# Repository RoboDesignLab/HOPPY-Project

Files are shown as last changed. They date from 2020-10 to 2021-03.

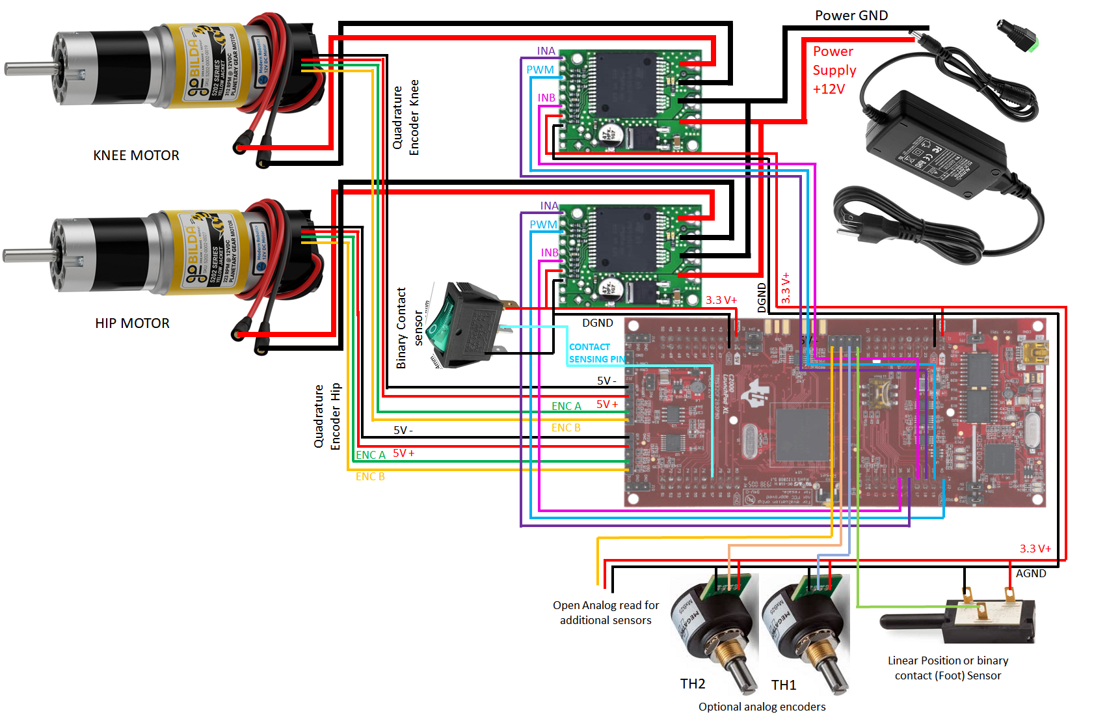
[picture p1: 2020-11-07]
wiring_diagram_HOPPY.png

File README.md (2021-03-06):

# ------------------------HOPPY-Project------------------------
## HOPPY: An Open-source Kit for Education with Dynamic Legged Robots
HOPPY 2
----------------------------------------------------------------------------------------------------------------------------
## CONTENTS OF THIS FILE
---------------------
* Introduction
* General Notes
* Setting up CCS 
* CAD 
* Simulator

## Introduction
------------
The project is an open-source, low-cost, robust, and modular kit for robotics education. The robot, HOPPY, dynamically hops around a fixed gantry. The kit targets lowering the barrier for studying dynamic robots and legged locomotion in real systems. Controlling dynamic motions in real robots present unique challenges to the software and hardware which are often overlooked in conventional robotics courses. This project describes the topics which can be studied using the kit, lists its components, discusses best practices for implementation, presents results from experiments with the simulator and the real system, and suggests further improvements. HOPPY was utilized as the topic of a semester-long project for the Robot Dynamics and Control course at the University of Illinois at Urbana-Champaign. Students provided a positive feedback from the hands-on activities during the course and the instructors will continue to develop and improve the kit for upcoming semesters.

Find out more in our overview paper: https://arxiv.org/pdf/2010.14580.pdf

Assembly instructions can be found here: https://youtu.be/CDxhdjob2C8

See the robot in action here:
https://youtu.be/_lbKIpiRWKI
https://www.youtube.com/watch?v=AvJIx4CQarM

-----------------------------------------------------------------------------------------------------------------------------
## General Notes
-------------
DO NOT run the given code to the motors while they are attached to the leg. This code is meant to show a given code flow and test the motors, board, and program setup. Clamp the motors down and run the code on them externally. 

Depending on how the leg is assembled, you may need to adjust the lengths used in the code. More instructions re inside the general definitions section of the program.

----------------------------------------------------------------------------------------------------------------------------
## Setting up Code Composer Studio (CCS) and the programming enviroment
--------------------------------------------------------------------
CCS is the IDE for TI products and is an easy to sude system. A introduction to CCS can be found at the following link: https://www.youtube.com/watch?v=11lsNYW7zkw&ab_channel=CodeComposer

Hoppy was implemented using version 8 of CCS which can be downloaded at the following link: http://software-dl.ti.com/ccs/esd/documents/ccs_downloads.html. The instructions for installing the software can be found at the second link. 

Once CCS in installed, unzip the Blinky_rtos_FLASHCCS8.zip folder and open the project in CCS. This project should blink an LED on the board after it is flashed onto the board. cpu01_main.c is the main file that you will be working in; this is also the file that you should be in when you build and debug the program.

Once the programming enviroment is working, the file cpu01_main_EXAMPLE.c can be coppied into cpu01_main.c. This program is a starting point for the user to program. It includes an intuitive code structure, working PD control on the hip and knee motors, and contact sensing (analog and binary). The instructions to use the code setup and the different sensing options is in the file with line numbers for each part in the code. 

The wiring diagram that shows how hook up the system is also included in the folder.

----------------------------------------------------------------------------------------------------------------------------
## CAD
---

The CAD models of the entire setup are inlcuded in SolidWorks and .STEP formats. Video  instructions for mechanical assembly can found at the following link: https://youtu.be/CDxhdjob2C8

The Bill of Materials (BOM), a complete list of components and quantities, is also listed in the folder. 

-----------------------------------------------------------------------------------------------------------------------------
## Simulator
---------

### Requirement
MATLAB and MATLAB optimization toolbox

### Installation
There is no need to install external packages.

### Usage
Navigate to the folder "Simulator_MATLAB" and set the working directory of MATLAB to be this directory. To start the simulation, run the file
```
...\Simulator_MATLAB\MAIN.m
```
If the code works properly, the following GUI will show up and a video file will be generated.



Please refer to the Code_Instruction.pdf file to navigate through each component of this simulator

If you encounter any problems regarding the simulator, please raise an issue under this repo.

Enjoy!
-----------------------------------------------------------------------------------------------------------------------------

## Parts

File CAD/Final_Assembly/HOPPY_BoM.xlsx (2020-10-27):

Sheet: Base
Index | Part Number | Quantity | Price per unit (USD) | Link
0.1 | 1140-0006-0144 | 1 | 12.99 | https://www.gobilda.com/1140-series-aluminum-baseplate-6mm-thickness-144mm-diameter/
0.2 | 4103-0032-0144 | 1 | 3.89 | https://www.gobilda.com/4103-series-gotube-144mm-length/
0.3 | 1604-0043-0032 | 2 | 12.99 | https://www.gobilda.com/1604-series-2-side-2-post-pillow-block-32mm-bore/
0.4 | 1500-0010-0032 | 1 | 0.1658333333 | https://www.gobilda.com/1500-series-plastic-spacer-32mm-id-x-34mm-od-1mm-thickness-12-pack/
0.5 | 1506-0032-0004 | 1 | 1.495 | https://www.gobilda.com/1506-series-32mm-id-spacer-36mm-od-4mm-length-2-pack/
0.6 | 1506-0032-0006 | 2 | 1.645 | https://www.gobilda.com/1506-series-32mm-id-spacer-36mm-od-6mm-length-2-pack/
0.7 | 2800-0004-0010 | 4 | 0.1356 | https://www.gobilda.com/2800-series-zinc-plated-steel-socket-head-screw-m4-x-0-7mm-10mm-length-25-pack/
0.8 | 98035A102 | 4 | 0.472 | https://www.mcmaster.com/98035A102/
0.9 | 2802-0004-0008 | 4 | 0.1276 | https://www.gobilda.com/2802-series-zinc-plated-steel-button-head-screw-m4-x-0-7mm-8mm-length-25-pack/

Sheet: Link 1
Index | Part Number | Quantity | Price per unit (USD) | Link | Notes
1.1 | 1123-0048-0144 | 2 | 4.29 | https://www.gobilda.com/1123-series-pattern-plate-1-x-5-hole-48-x-144mm/
1.2 | 1121-0003-0096 | 1 | 2.89 | https://www.gobilda.com/1121-series-low-side-u-channel-3-hole-96mm-length/
1.3 | 2803-0039-0007 | 2 | 1.995 | https://www.gobilda.com/2803-series-stainless-steel-threaded-plate-39-7-2-pack/
1.4 | 1502-0006-0020 | 4 | 0.2975 | https://www.gobilda.com/1502-series-4mm-id-spacer-6mm-od-2mm-length-4-pack/
1.5 | 1502-0006-0030 | 4 | 0.3225 | https://www.gobilda.com/1502-series-4mm-id-spacer-6mm-od-3mm-length-4-pack/
1.6 | 2800-0004-0010 | 20 | 0.1356 | https://www.gobilda.com/2800-series-zinc-plated-steel-socket-head-screw-m4-x-0-7mm-10mm-length-25-pack/
1.7 | 1401-0043-0032 | 2 | 5.99 | https://www.gobilda.com/1401-series-2-side-2-post-clamping-mount-43mm-width-32mm-bore/
1.8 | 1506-0032-0004 | 4 | 1.495 | https://www.gobilda.com/1506-series-32mm-id-spacer-36mm-od-4mm-length-2-pack/
1.9* | 1400-0032-0032 | 2 | 5.99 | https://www.gobilda.com/1400-series-1-side-2-post-clamping-mount-32mm-bore/ | *Only required if utilizing encoder on jount 2.
1. 10 | 4103-0032-0043 | 2 | 2.99 | https://www.gobilda.com/4103-series-gotube-43mm-length/
1.11 | 1603-0032-0032 | 2 | 12.99 | https://www.gobilda.com/1603-series-face-thru-hole-pillow-block-32mm-bore/
1.12 | 4103-0032-0912 | 1 | 11.69 | https://www.gobilda.com/4103-series-gotube-912mm-length/
1.14 | 1502-0006-0100 | 4 | 0.41 | https://www.gobilda.com/1502-series-4mm-id-spacer-6mm-od-10mm-length-4-pack/
1.15 | 2800-0004-0018 | 4 | 0.1556 | https://www.gobilda.com/2800-series-zinc-plated-steel-socket-head-screw-m4-x-0-7mm-18mm-length-25-pack/

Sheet: Link 2
Index | Part Number | Quantity | Price per unit (USD) | Link | Notes
2.1 | 5202-0002-0027 | 1 | 39.99 | https://www.gobilda.com/5202-series-yellow-jacket-planetary-gear-motor-26-9-1-ratio-223-rpm-3-3-5v-encoder/
2.2 | 1201-0043-0002 | 1 | 5.99 | https://www.gobilda.com/1201-series-quad-block-pattern-mount-43-2/
2.3 | 2802-0004-0008 | 8 | 0.1276 | https://www.gobilda.com/2802-series-zinc-plated-steel-button-head-screw-m4-x-0-7mm-8mm-length-25-pack/
2.4 | 1111-0004-0001 | 1 | 5.99 | https://www.gobilda.com/1111-series-angle-pattern-bracket-4-1/
2.5 | 2800-0004-0010 | 4 | 0.1356 | https://www.gobilda.com/2800-series-zinc-plated-steel-socket-head-screw-m4-x-0-7mm-10mm-length-25-pack/
2.6 | 1108-0001-0001 | 1 | 1.99 | https://www.gobilda.com/1108-series-flat-pattern-bracket-1-1/
2.7 | 1309-0016-1006 | 1 | 5.99 | https://www.gobilda.com/1309-series-sonic-hub-6mm-d-bore/
2.8 | 1401-0043-0032 | 1 | 5.99 | https://www.gobilda.com/1401-series-2-side-2-post-clamping-mount-43mm-width-32mm-bore/
2.9 | 1123-0048-0144 | 2 | 4.29 | https://www.gobilda.com/1123-series-pattern-plate-1-x-5-hole-48-x-144mm/
2. 10 | 2800-0004-0010 | 4 | 0.1356 | https://www.gobilda.com/2800-series-zinc-plated-steel-socket-head-screw-m4-x-0-7mm-10mm-length-25-pack/
2.11 | 5202-0002-0019 | 1 | 39.99 | https://www.gobilda.com/5202-series-yellow-jacket-planetary-gear-motor-19-2-1-ratio-312-rpm-3-3-5v-encoder/
2.12 | 1111-0004-0001 | 1 | 5.99 | https://www.gobilda.com/1111-series-angle-pattern-bracket-4-1/
2.13 | 1604-0043-0032 | 1 | 12.99 | https://www.gobilda.com/1604-series-2-side-2-post-pillow-block-32mm-bore/
2.14 | 2800-0004-0010 | 4 | 0.1356 | https://www.gobilda.com/2800-series-zinc-plated-steel-socket-head-screw-m4-x-0-7mm-10mm-length-25-pack/
2.15 | 1108-0001-0001 | 1 | 1.99 | https://www.gobilda.com/1108-series-flat-pattern-bracket-1-1/
2.16 | 2802-0004-0008 | 4 | 0.1276 | https://www.gobilda.com/2802-series-zinc-plated-steel-button-head-screw-m4-x-0-7mm-8mm-length-25-pack/
2.17 | 3414-1006-0016 | 1 | 7.99 | https://www.gobilda.com/3414-series-5mm-htd-pitch-set-screw-pinion-timing-belt-pulley-6mm-d-bore-16-tooth/
2.18 | 1201-0043-0002 | 1 | 5.99 | https://www.gobilda.com/1201-series-quad-block-pattern-mount-43-2/
2.19 | 2800-0004-0010 | 8 | 0.1356 | https://www.gobilda.com/2800-series-zinc-plated-steel-socket-head-screw-m4-x-0-7mm-10mm-length-25-pack/

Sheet: Link 3
Index | Part Number | Quantity | Price per unit (USD) | Link | Notes
3.1 | 1120-0001-0048 | 1 | 1.99 | https://www.gobilda.com/1120-series-u-channel-1-hole-48mm-length/
3.2 | 1205-0001-0003 | 1 | 2.495 | https://www.gobilda.com/1205-series-dual-block-mount-1-3-2-pack/
3.3 | 1502-0005-0100 | 2 | 1.2475 | https://www.gobilda.com/1502-series-4mm-id-spacer-5mm-od-10mm-length-4-pack/
3.4 | 2800-0004-0018 | 2 | 0.1556 | https://www.gobilda.com/2800-series-zinc-plated-steel-socket-head-screw-m4-x-0-7mm-18mm-length-25-pack/
3.5 | 2802-0004-0008 | 2 | 0.1276 | https://www.gobilda.com/2802-series-zinc-plated-steel-button-head-screw-m4-x-0-7mm-8mm-length-25-pack/
3.6 | 1607-0041-0615 | 1 | 6.99 | https://www.gobilda.com/1607-series-idler-bearing-6mm-id-x-15mm-od-41mm-length/ | This part already contains the bearings shown in the assembly video.
3.7 | 2800-0004-0010 | 2 | 0.1356 | https://www.gobilda.com/2800-series-zinc-plated-steel-socket-head-screw-m4-x-0-7mm-10mm-length-25-pack/
3.8 | 3412-0009-0295 | 1 | 4.79 | https://www.gobilda.com/3412-series-5mm-htd-pitch-timing-belt-9mm-width-295mm-pitch-length-59-tooth/
3.9 | 2102-0008-0050 | 1 | 2.79 | https://www.gobilda.com/2102-series-stainless-steel-rex-shaft-8mm-diameter-50mm-length/
3. 10 | 1309-0016-4008 | 2 | 5.99 | https://www.gobilda.com/1309-series-sonic-hub-8mm-rex-bore/
3.11 | 1108-0001-0001 | 2 | 1.99 | https://www.gobilda.com/1108-series-flat-pattern-bracket-1-1/
3.12 | 2802-0004-0008 | 8 | 0.1276 | https://www.gobilda.com/2802-series-zinc-plated-steel-button-head-screw-m4-x-0-7mm-8mm-length-25-pack/
3.13 | 2803-0039-0007 | 2 | 1.995 | https://www.gobilda.com/2803-series-stainless-steel-threaded-plate-39-7-2-pack/
3.14 | 2803-0039-0007 | 2 | 1.995 | https://www.gobilda.com/2803-series-stainless-steel-threaded-plate-39-7-2-pack/
3.15 | 2802-0004-0008 | 4 | 0.1276 | https://www.gobilda.com/2802-series-zinc-plated-steel-button-head-screw-m4-x-0-7mm-8mm-length-25-pack/
3.16 | 1501-0006-0430 | 1 | 0.91 | https://www.gobilda.com/1501-series-m4-x-0-7mm-standoff-6mm-od-43mm-length-4-pack/ | This part is missing in the assembly video. This is the shaft for the belt tensioner.

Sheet: Link 4
Index | Part Number | Quantity | Price per unit (USD) | Link | Notes
4.1 | 1502-0005-0100 | 2 | 1.2475 | https://www.gobilda.com/1502-series-4mm-id-spacer-5mm-od-10mm-length-4-pack/
4.2 | 2800-0004-0018 | 2 | 0.1556 | https://www.gobilda.com/2800-series-zinc-plated-steel-socket-head-screw-m4-x-0-7mm-18mm-length-25-pack/
4.3 | 1402-0043-0014 | 1 | 4.99 | https://www.gobilda.com/1402-series-2-side-1-post-clamping-mount-43mm-width-14mm-bore/
4.4 | 1400-0032-0014 | 2 | 5.99 | https://www.gobilda.com/1400-series-1-side-2-post-clamping-mount-14mm-bore/
4.5 | Rubber Cap | 1 | 0.4745 | https://www.amazon.com/uxcell-Furniture-Protector-Prevent-Scratches/dp/B07MTLFY8M | Chair Leg Tips Caps 14mm 9/16 Inch Anti Slip Rubber Furniture Feet Protector
4.6 | 4100-1214-0200 | 1 | 1.69 | https://www.gobilda.com/4100-series-aluminum-tube-12mm-id-x-14mm-od-200mm-length/
4.7 | 1102-0005-0040 | 2 | 1.045 | https://www.gobilda.com/1102-series-flat-beam-5-hole-40mm-length-2-pack/
4.8 | 2800-0004-0010 | 6 | 0.1356 | https://www.gobilda.com/2800-series-zinc-plated-steel-socket-head-screw-m4-x-0-7mm-10mm-length-25-pack/
4.9 | 1200-0032-0001 | 1 | 3.99 | https://www.gobilda.com/1200-series-1-side-2-post-pattern-mount-32-1/
4. 10 | 1505-0032-0080 | 1 | 3.99 | https://www.gobilda.com/1505-series-32mm-od-counterbored-pattern-spacer-8mm-length/
4.11 | 1611-0514-4008 | 2 | 2.995 | https://www.gobilda.com/1611-series-flanged-ball-bearing-8mm-rex-id-x-14mm-od-5mm-thickness-2-pack/
4.12 | 2802-0004-0008 | 4 | 0.1276 | https://www.gobilda.com/2802-series-zinc-plated-steel-button-head-screw-m4-x-0-7mm-8mm-length-25-pack/
4.13 | 2800-0004-0010 | 4 | 0.1356 | https://www.gobilda.com/2800-series-zinc-plated-steel-socket-head-screw-m4-x-0-7mm-10mm-length-25-pack/
4.14 | 3411-0014-0024 | 1 | 7.99 | https://www.gobilda.com/3411-series-5mm-htd-pitch-aluminum-hub-mount-timing-belt-pulley-14mm-bore-24-tooth/
4.15 | 2915-0001-0001 | 2 | 4.99 | https://www.gobilda.com/extension-spring-8mm-od-6-8kg-max-load-80-120mm-length/ | This part is missing in the assembly video. This is the spring for the knee joint.

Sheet: Electronics
Index | Part Number | Quantity | Price per unit (USD) | Link | Notes
E1 | VNH5019 | 2 | 24.95 | https://www.pololu.com/product/1451
E2 | F28379D | 1 | 33.79 | https://www.ti.com/tool/LAUNCHXL-F28379D?gclsrc=aw.ds
E2 | 12V 10A Power Supply | 1 | 19.99 | https://www.amazon.com/dp/B07MXXXBV8

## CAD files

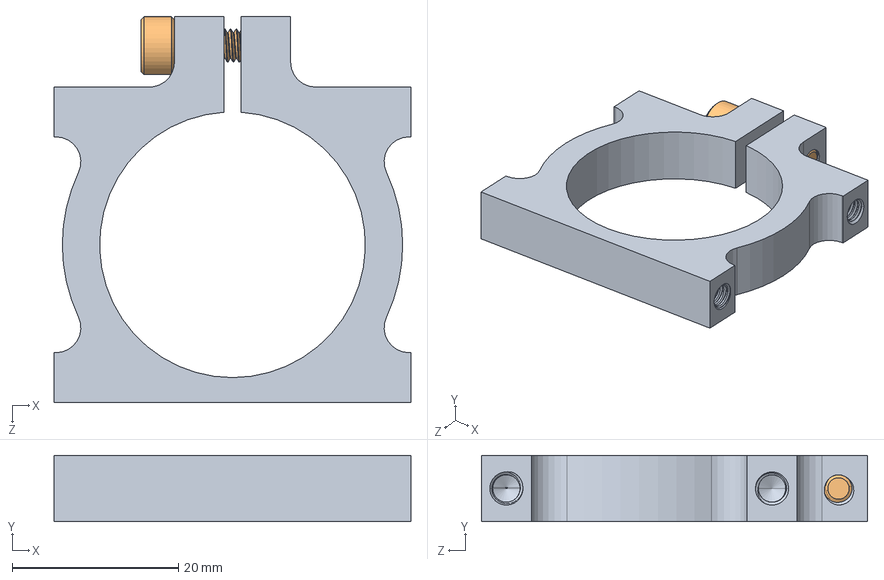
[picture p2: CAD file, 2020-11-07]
CAD/Final_Assembly/Base/1401-0043-0032 assembly.SLDASM
43.0 x 8.00 x 46.5 mm
1401-0043-0032.STEP
2800-0004-0014_90128A207.STEP

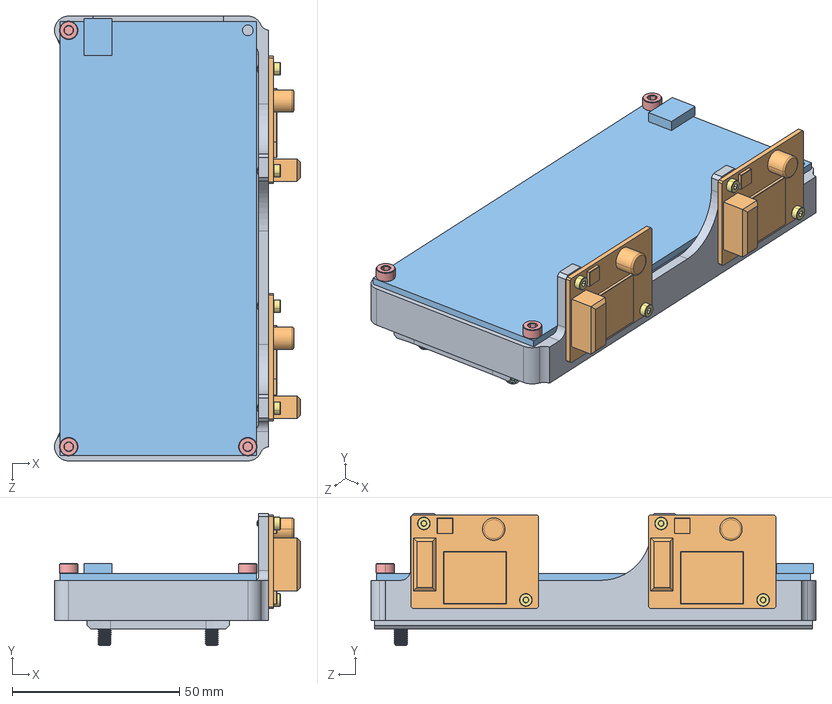
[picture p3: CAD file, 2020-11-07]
CAD/Final_Assembly/Electronics/Electronics_Assembly.STEP
73.5 x 39.5 x 132.9 mm
3DPrinted_Electronics_Support
Pololu_Motor_Carrier_VNH5019 x 2
TI_Microcontroller_LAUNCHXL-F28379D
91290A119_BLACK-OXIDE CLASS 12.9 SOCKET HEAD CAP SCREW_91290A119 x 3
90591A121_ZINC-PLATED STEEL HEX NUT_90591A121 x 3
91290A012_BLACK-OXIDE CLASS 12.9 SOCKET HEAD CAP SCREW_91290A012 x 4

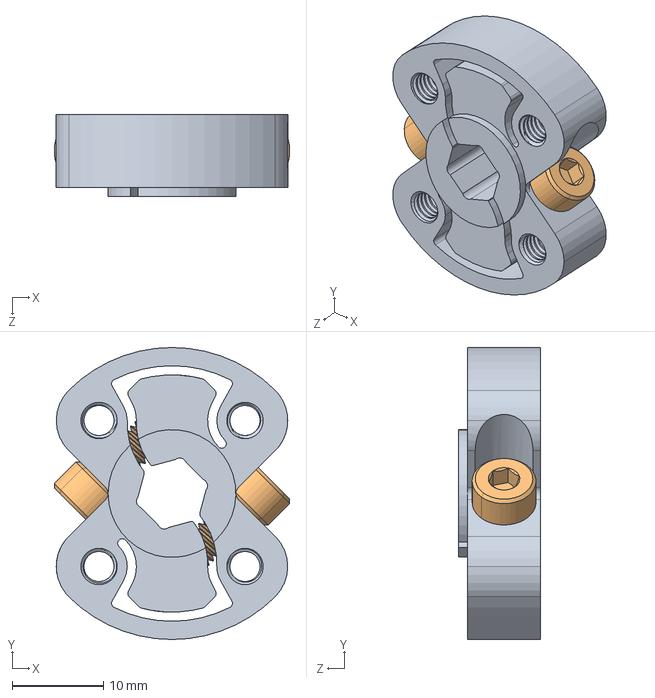
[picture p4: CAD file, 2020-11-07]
CAD/Final_Assembly/Link3/1309-0016-4008 assembly.SLDASM
25.8 x 32.0 x 9.00 mm
1309-0016-4008.STEP
2800-0004-0014_90128A207.STEP x 2

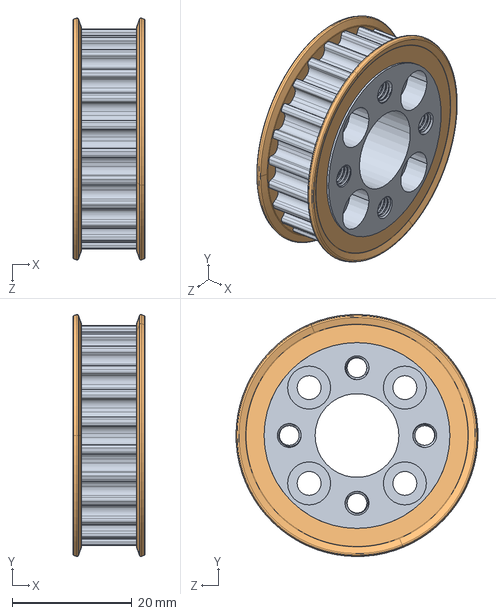
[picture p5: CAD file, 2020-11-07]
CAD/Final_Assembly/Link4/3411-0014-0024 Assembly.SLDASM
12.1 x 40.4 x 40.4 mm
3411-0014-0024 Body.STEP
3411-0014-0024 Ring.STEP x 2

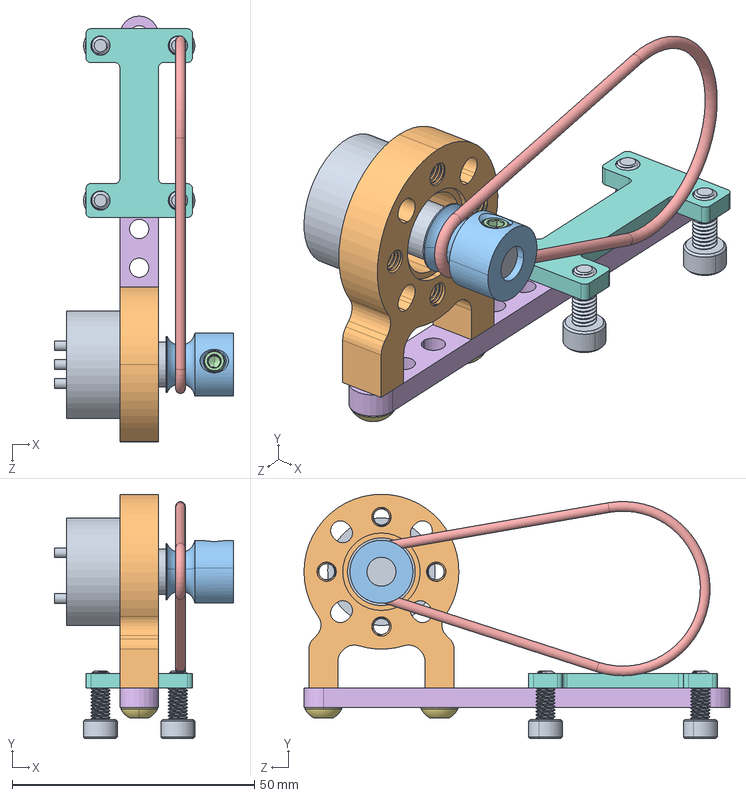
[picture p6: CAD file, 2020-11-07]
CAD/Final_Assembly/Add-ons/Encoder1_Assembly.SLDASM
37.1 x 50.5 x 88.0 mm
6127V1A360L.5 Non-Contacting Hall Effect
3401-0006-0008.STEP
2806-0005-0004_91390A117.STEP
Round_Belt

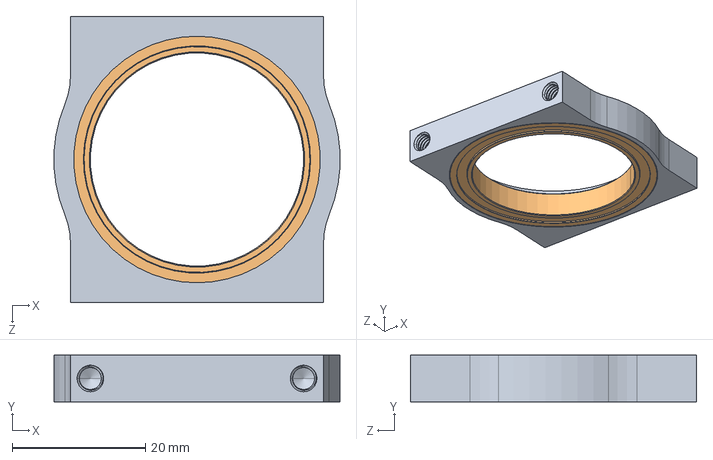
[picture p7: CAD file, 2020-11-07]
CAD/Final_Assembly/Link1/1604-0043-0032 assembly.SLDASM
42.9 x 7.00 x 43.0 mm
1604-0043-0032.STEP
1601-0039-00032.STEP

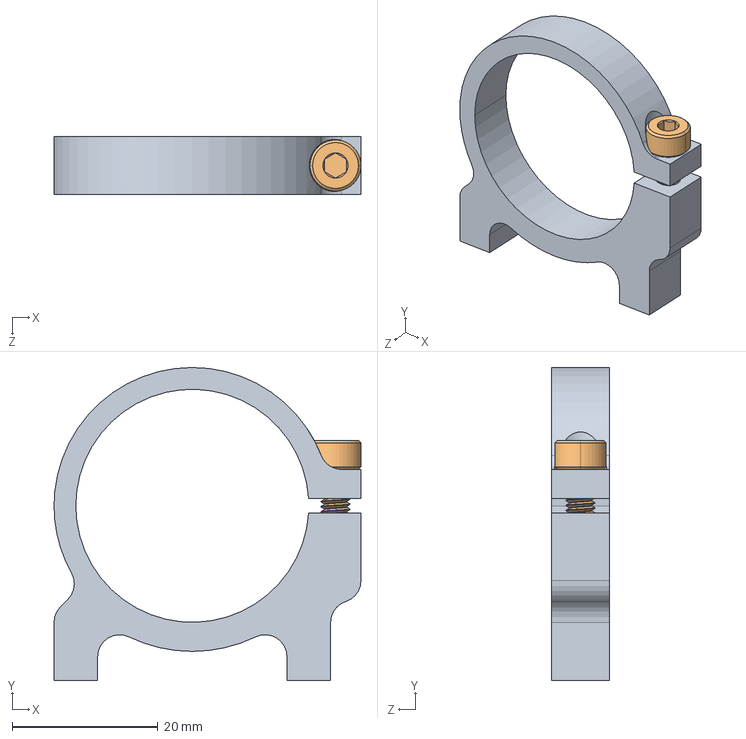
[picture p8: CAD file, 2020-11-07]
CAD/Final_Assembly/Link2/1400-0032-0032 assembly.SLDASM
42.2 x 43.0 x 8.00 mm
1400-0032-0032.STEP
2800-0004-0012_90128A207.STEP

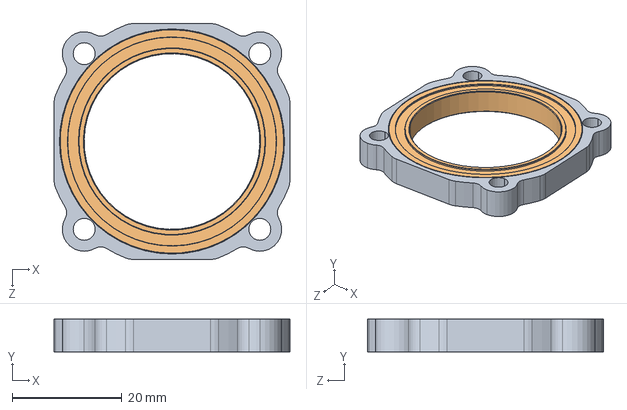
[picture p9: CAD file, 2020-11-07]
CAD/Final_Assembly/Link2/1603-0032-0032 assembly.SLDASM
43.0 x 6.00 x 43.0 mm
1603-0032-0032.STEP
1601-0039-00032.STEP

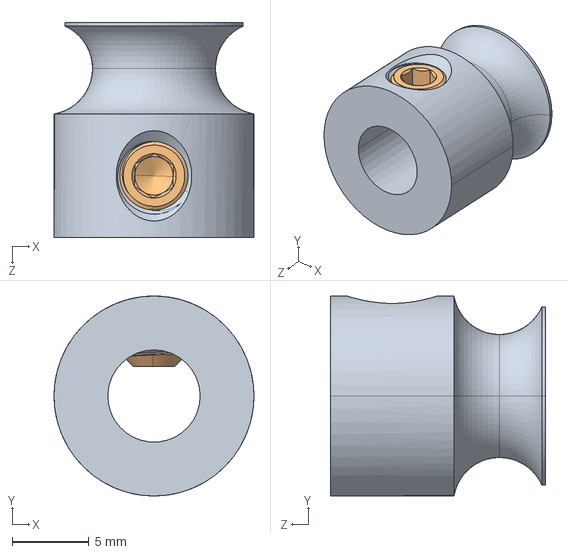
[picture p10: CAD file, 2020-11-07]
CAD/Final_Assembly/Add-ons/3401-0006-0008 assembly.SLDASM
13.0 x 13.0 x 14.0 mm
3401-0006-0008.STEP
2806-0005-0004_91390A117.STEP

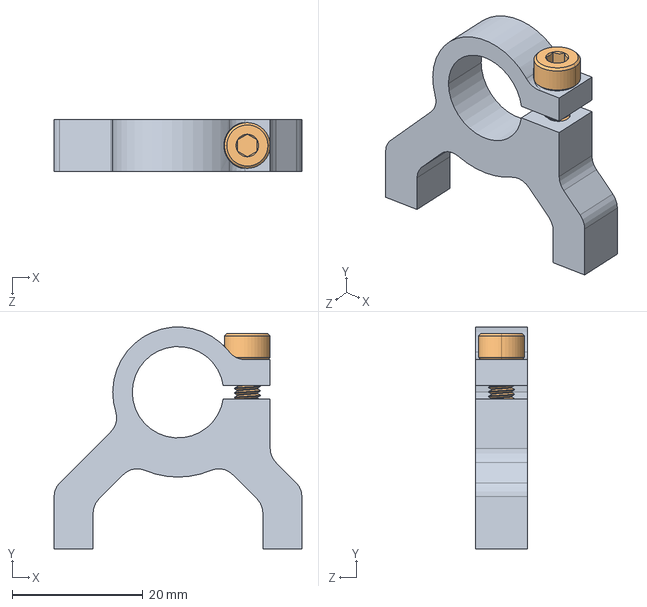
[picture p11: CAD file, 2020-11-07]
CAD/Final_Assembly/Link4/1400-0032-0014 assembly.SLDASM
38.0 x 34.0 x 8.00 mm
1400-0032-0014.STEP
2800-0004-0012_90128A207.STEP

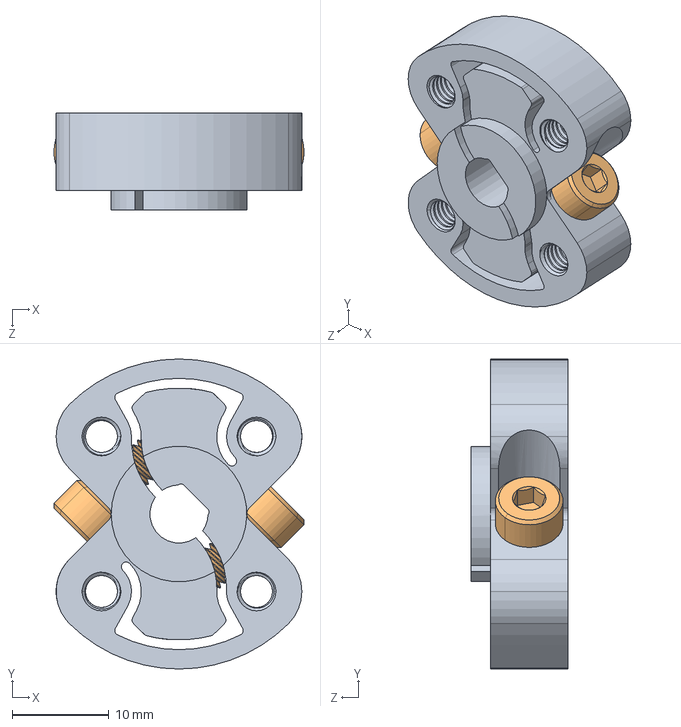
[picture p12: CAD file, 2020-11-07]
CAD/Final_Assembly/Link3/1309-0016-1006 assembly.SLDASM
25.8 x 32.0 x 10.0 mm
1309-0016-1006.STEP
2800-0004-0014_90128A207.STEP x 2

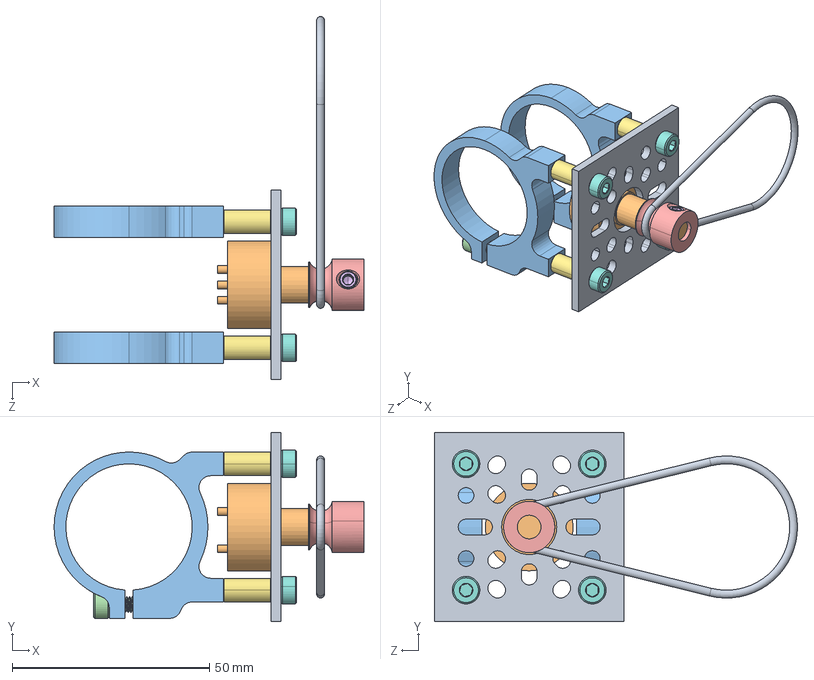
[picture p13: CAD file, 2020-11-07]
CAD/Final_Assembly/Add-ons/Encoder2_Assembly.SLDASM
78.5 x 48.0 x 92.0 mm
6127V1A360L.5 Non-Contacting Hall Effect
1400-0032-0032.STEP x 2
2800-0004-0012_90128A207.STEP x 2
3401-0006-0008.STEP
2806-0005-0004_91390A117.STEP
Round_Belt

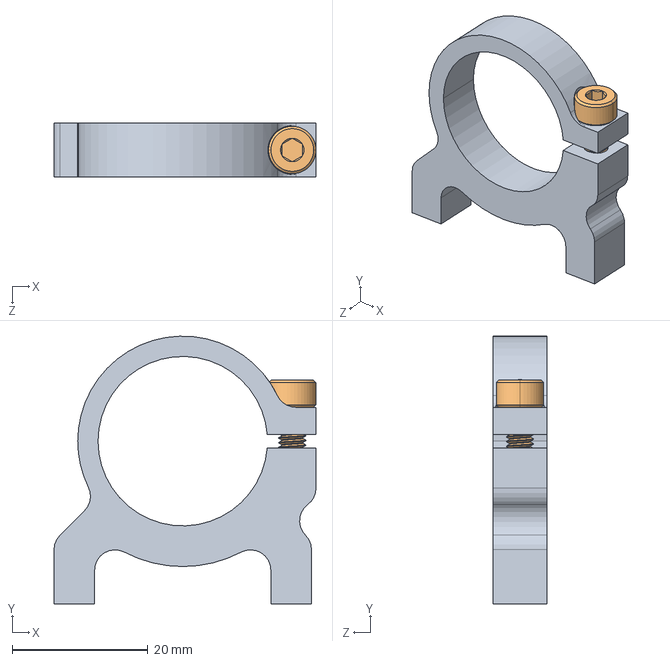
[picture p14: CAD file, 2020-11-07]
CAD/Final_Assembly/Link2/1400-0032-0025 assembly.SLDASM
38.7 x 39.5 x 8.00 mm
1400-0032-0025.STEP
2800-0004-0010_90128A207.STEP

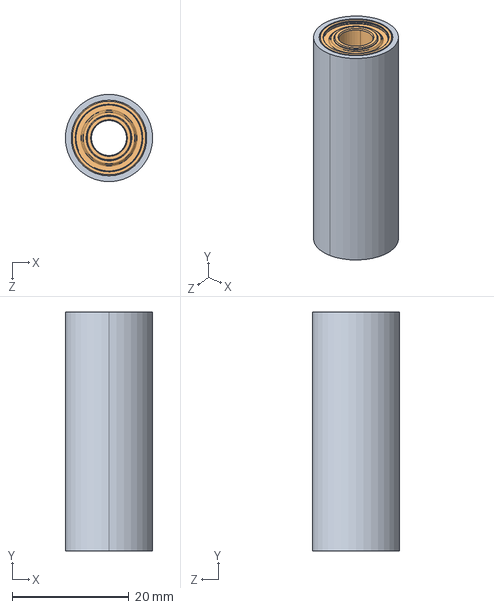
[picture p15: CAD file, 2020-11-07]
CAD/Final_Assembly/Link3/1607-0041-0615 assembly.SLDASM
15.0 x 41.0 x 15.0 mm
1607-0041-0615.STEP
1600-0513-0006.STEP x 2

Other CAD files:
CAD/Final_Assembly/Add-ons/1102-0011-0088.SLDPRT
CAD/Final_Assembly/Add-ons/1123-0048-0048.SLDPRT
CAD/Final_Assembly/Add-ons/1200-0024-0001.SLDPRT
CAD/Final_Assembly/Add-ons/1502-0006-0120.SLDPRT
CAD/Final_Assembly/Add-ons/2803-0039-0007.SLDPRT
CAD/Final_Assembly/Add-ons/2803-0039-0022.SLDPRT
CAD/Final_Assembly/Add-ons/6127V1A360L.5 Non-Contacting Hall Effect.SLDPRT
CAD/Final_Assembly/Add-ons/Round_Belt.SLDPRT
CAD/Final_Assembly/Base/1140-0006-0144.SLDPRT
CAD/Final_Assembly/Base/1500-0010-0032.SLDPRT
CAD/Final_Assembly/Base/1506-0032-0004.SLDPRT
CAD/Final_Assembly/Base/1506-0032-0006.SLDPRT
CAD/Final_Assembly/Base/4103-0032-0144.SLDPRT
CAD/Final_Assembly/Base/4103-0032-0192.SLDPRT
CAD/Final_Assembly/Electronics/3DPrinted_Electronics_Support.SLDPRT
CAD/Final_Assembly/Electronics/Electronics_Assembly.SLDASM
CAD/Final_Assembly/Electronics/Pololu_Motor_Carrier_VNH5019.SLDPRT
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

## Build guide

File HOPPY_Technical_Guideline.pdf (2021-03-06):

## HOPPY: The Technical Guideline

Joao Ramos¹,2

, Yanran Ding¹

, Young-woo Sim¹

, Kevin Murphy¹

, and Daniel Block²

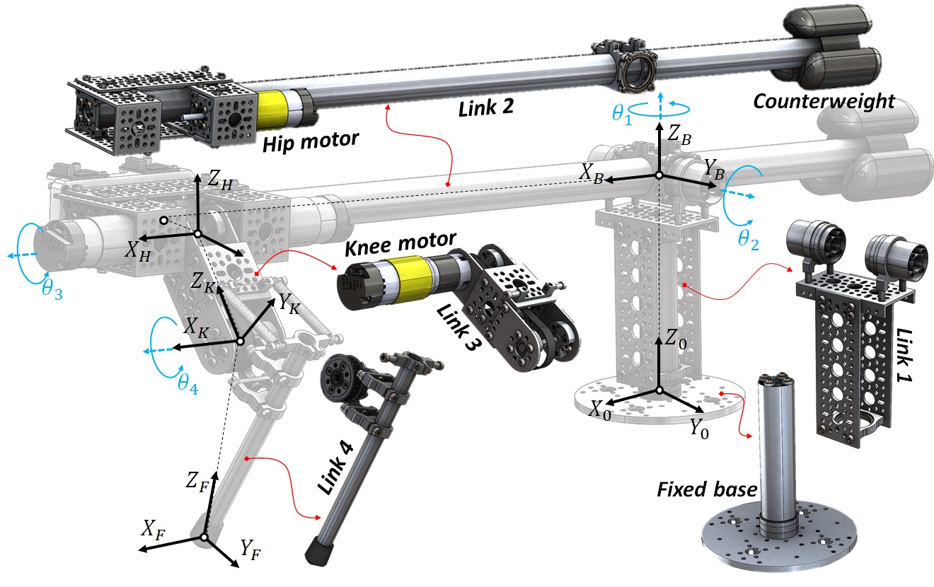
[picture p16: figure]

Fig. 1. Kinematic transformations and the five rigid-bodies which compose HOPPY. The first two joints (θ1 and θ2) are passive while joints three and four are driven by electric motors.

This document is a technical manual that describes the implementation details of HOPPY kit in the Robot Dynamics and Control course at UIUC. The content presented here should be treated as a pedagogical guideline, and therefore could be altered and adapted depending on the curriculum design.
When HOPPY hops around the gantry, it behaves as a hybrid system [12]. This means that the dynamics have continuous evolution when the robot is on the ground (stance phase) or airborne (flight phase), but it is interrupted by discrete events when the foot hits the ground (touchdown) or when it takes-off. In this section we describe the equations of motion during stance and flight phases, as well as the transitions between the two.
I. KINEMATICS

The kinematic transformations of HOPPY are shown in fig. 1. The robot consists of a two degrees-of-freedom (DoF) active leg attached to a supporting gantry with two additional DoF’s. The origin coordinate frame X0Y0Z0 at the base of the rotating gantry is fixed to the ground. Joints θ1,2 are passive (no actuation) while joints θ3,4 are driven by electric motors described in section III. When hopping, the robot can translate horizontally around θ1 and vertically around θ2. If the gantry length LB is sufficiently long, the robot moves approximately in a 2D (Sagittal) plane [12]. The transformation between coordinate frames is described by

Authors are with the 1Department of Mechanical Science and Engineering and the 2Department of Electrical & Computer Engineering at the University of Illinois at Urbana-Champaign, USA.
jlramos@illinois.edu

the Homogeneous Transformation Matrices (HTM) given by T

k
k+1, which converts a vector p

k+1 expressed in coordinate frame k + 1 into a vector p

k
expressed in coordinate frame k [8]:

p

k = T

k
k+1p

k+1 =

Rk
k+1 d

k
01×3 1
p

k+1
. | (1)

Where the term 01×3 represents a matrix of zeros with 1 rows and 3 columns. The HTM is composed of a rotation matrix Rk
k+1 ∈ SO(3) and a Cartesian translation d

k ∈ R

3
represented in frame k. The position p

0
foot of the foot in respect to the base frame expressed in world-fixed coordinates is
p

0
foot
1
= T

0
F
p

F
foot
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
03×1
1
. (2)

The complete kinematic transformations for HOPPY are described in the provided MATLAB-based simulator.

II. RIGID-BODY DYNAMICS DURING FLIGHT PHASE
The robot state vector is given by the collection of joint
angles q = [θ1 | θ2 | θ3 | θ4]

T
and their time rate of change q˙. When the foot is not contacting the ground and the robot is airborne, the equation of motion (EoM) of the robot is given by the well-known manipulator equation
M(q)¨q + C(q, q˙) ˙q + G(q) = τ, | (3)

which is derived from energy principles using the system’s Lagragian as described in [8]. Where M(q) represents the symmetric and positive definite inertia matrix as a function of the configuration, C(q, q˙) is the Coriollis and centrifugal forces matrix, G(q) is the vector of torques due to gravity, and τ is the vector of input torques. The system is underactuated because the first two joints are passive (τ1 = τ2 = 0), and thus, there are four overall DoF but only two inputs [9]. The input vector is given by

τ = Beu +

0
0
0
τs(θ4)

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
τs(θ4)

, (4)

where Be is a selection matrix which maps the input torques u to the full system dynamics and τs(θ4) represents the torque exerted by the knee spring as a function of the knee angle θ4. The robot controller can only select torques for the hip τH and knee τK in order to hop around the gantry. The spring attached in parallel with the knee alleviates the joint’s torque requirements for hopping. The expression for τs(θ4) and the rigid-body parameters for each link mass, center of mass (CoM) position, and inertia tensor are provided in the instructions.

III. ACTUATOR DYNAMICS MODEL
Equation (4) assumes that the actuators are perfect torque sources which can generate arbitrary torque profiles. This assumption may be reasonable for simulation, but in reality the actuator dynamics play a major role in the overall system behavior and stability [6]. Sophisticated drivers can rapidly regulate the current i in the motor coils, which is approximately linearly proportional to the output torque τ = kT i if the steel saturation is neglected (kT is the motor constant [3]). However, such drivers are expensive (over $100) and here we employ the $25 Pololu VNH5019 in our kit, which can only control the voltage V across the motor terminals. In this situation, the back-electromotive force (back-EMF) significantly effects the actuator behavior. On the other hand, this limitation provides a valuable opportunity for students to explore how the actuator performance affects the overall dynamics. The model for a brushed and brushless electric motor assuming negligible coil inductance is given by [6]
V = Rwi + kvN ˙θ, | (5)

¨θN²
Ir = kT i. | (6)

Where Rw is the coil resistance, kv is the speed constant in V s
rad ,

˙θ is the joint velocity (after the gear box), Ir is the motor rotor inertia, and N is the gearbox speed reduction ratio. The hip and knee actuators in HOPPY utlize identical electric motors, but with different gear ratios (NH = 26.9 and NK = 28.8). Equation (3) is augmented to include the actuator dynamics using

(M(q) + Mr)¨q + (C(q, q˙) + BEMF ) ˙q + G(q) = τ. (7)

Where Mr is the inertial effect due to rotor inertia and BEMF is the (damping) term due to the back-EMF:

Mr = Ir

02×2 | 02×2

02×2

N²
H | 0
0 | N²
K

- , | (8)

BEMF =

kvkT
Rw
02×2 | 02×2

02×2

N²
H | 0
0 | N²
K

- , | (9)

and the updated selection matrix and control inputs are given by

Be =

kT
Rw

02×2
NH | 0
0 | NK

- , | (10)

u =

VH VK

T
, | (11)

which illustrates that the input to the system is the voltage applied to the motors, not the torque they produce. Actuators with large gearing ratios have high output inertia (due to the N²
term in (6)) and are usually non-backdrivable because of friction amplification. Thus, we select minimal reduction ratio in HOPPY to mitigate the effect of shock loads in the system during touchdown [4], [11]. Joint friction can have major (nonlinear) effects on the robot dynamics and models for stiction, dry coulomb friction, viscous friction, and more are suggested in [6] and can be included in the model.

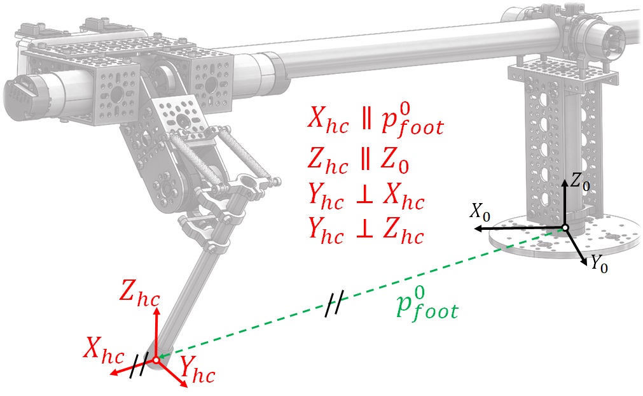
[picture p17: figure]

Fig. 2. The frame used for the holonomic constraint for non-slip condition. Frame XhcYhcZhc changes every time the robot establishes a new foothold and does not necessarily coincides with foot-fixed frame XF YF ZF .

IV. RIGID-BODY DYNAMICS DURING STANCE PHASE

Equations (3) and (7) are valid when the robot foot is not touching the ground. When contact occurs, the EoM must describe how the ground reaction forces (GRF) affect the robot motion. Contact mechanics are challenging to simulate in complex systems and commercial physics simulation engines, such as MuJoCo [10], employ different numerical techniques to approximate them. Two common approxima-tions are know as soft and hard contact models [12]. The soft contact model approximates the contact mechanics by modelling the ground as a spring and damper. Thus, the foot must penetrate the ground to generate contact forces. Because the ground is assumed to have high stiffness values, small deformations render large contact forces, and the solver may encounter numerical instability [2]. In contrast, the hard contact model, which is used in our simulator, does not allow the foot the to penetrate the ground. It includes a holonomic constraint which assumes that the foot does not slip in the Yhc and Zhc directions, shown in fig. 2, when in contact with the ground. However, the foot is allowed to slip in the Xhc direction, otherwise the system would be overconstrained. The Zhc axis is always vertical, axis Xhc is colinear with the line that connects the gantry base and the foot, and Yhc is perpendicular to these. Frame XhcYhcZhc changes every time the robot establishes a new foothold and does not necessarily coincides with foot-fixed frame XF YF ZF . We utilize the Jacobian Jhc ∈ R

2×4
to write a holonomic
constraint for the non-slip condition

Jhcq˙ =

vY hc

vZhc
=
0
0
. | (12)

Where vY hc and vZhc are the foot linear velocity in the Yhc and Zhc directions. Equation (12) is satisfied if [12]

Jhcq¨+ J˙
hcq˙ = 02×1 | (13)

is also satisfied. Moreover, when the robot pushes against the ground, it generates reaction forces FGRF = [FY hc FZhc]

T
which alter the EoM by J

T
hcFGRF . Finally, the complete stance dynamics is represented by the matrix equation which includes the manipulator equation plus the holonomic constraint:
M(q) −J

T
hc
Jhc 02×2

q¨

FGRF
=
τ − C(q, q˙) ˙q − G(q)
−J˙
hcq˙
. (14)

Hence, when solving the forward dynamics, the numeric integrator (MATLAB’s ode45()) takes the input vector u from the control law and calculates the joints acceleration q¨ and the resultant contact forces FGRF at every iteration.

V. FOOT IMPACT MODEL AT TOUCHDOWN

The impact dynamics are challenging to model realistically and they may cause numerical issues for the solver. Our simulator assumes a completely inelastic collision, which means that the foot comes to a complete stop after hitting the ground. And thus, the robot looses energy every time the foot impacts the ground [11]. This assumption implies that the impulsive impact forces remove energy from the system, and the velocity instantaneously changes from q˙

− at time
t

− before the impact to q˙
+ immediately after the impact at time t

+. However, because this discontinuous changes occurs instantaneously, the joint angles remain unchanged (q

− = q
+). To compute the robot velocity after the impact we integrate both sides of equation (14) between t

− and t
+.
Because the joint angles and control inputs do not change during impact we obtain [1], [12]

M( ˙q

+ − q˙

−) = J
T
hcFimp, | (15)

in addition to the constraint due to the inelastic collision Jhcq˙

+ = 0. We utilize these equations to write the impact map which defines the transition between the aerial phase described by the dynamic EOM (3) to the stance phase described by equation (14) [12]:
q˙

+
Fimp
=
M(q) −J

T
hc
Jhc 02×2

−1
M(q) ˙q

−

02×1

. (16)

Notice that the impact force Fimp is affected by the inverse of the inertia matrix, which is amplified by the reflected inertia of the rotors. Hence, actuators with high gear ratios will create large impact forces, and thus, HOPPY employs minimal gearing [11].

VI. NUMERICAL SIMULATION

A hybrid system is a dynamical system that exhibits both continuous and discrete behavior. HOPPY displays continuous dynamics during flight phase or stance phase, but experiences discontinuous transitions between the two. To simulate hybrid systems, solvers like MATLAB’s ode45() utilize guard functions to flag the transitions between con-tinuum phases. For instance, the numerical simulation starts with the aerial phase dynamics and is interrupted when the touchdown guard function (foot height) cross a certain threshold (ground height), or: p

0
Zfoot(t) = 0. Similarly, the robot takes-off the ground when the vertical component of the ground reaction force reaches a value equal to zero: FZGRF (t) = 0. This sequence is shown in fig. 3. The simulator starts in the aerial phase and runs the integration for n hops, which is defined by the number of the transitions between the stance to aerial phase. The simulator is described in detail in the provided instructions.

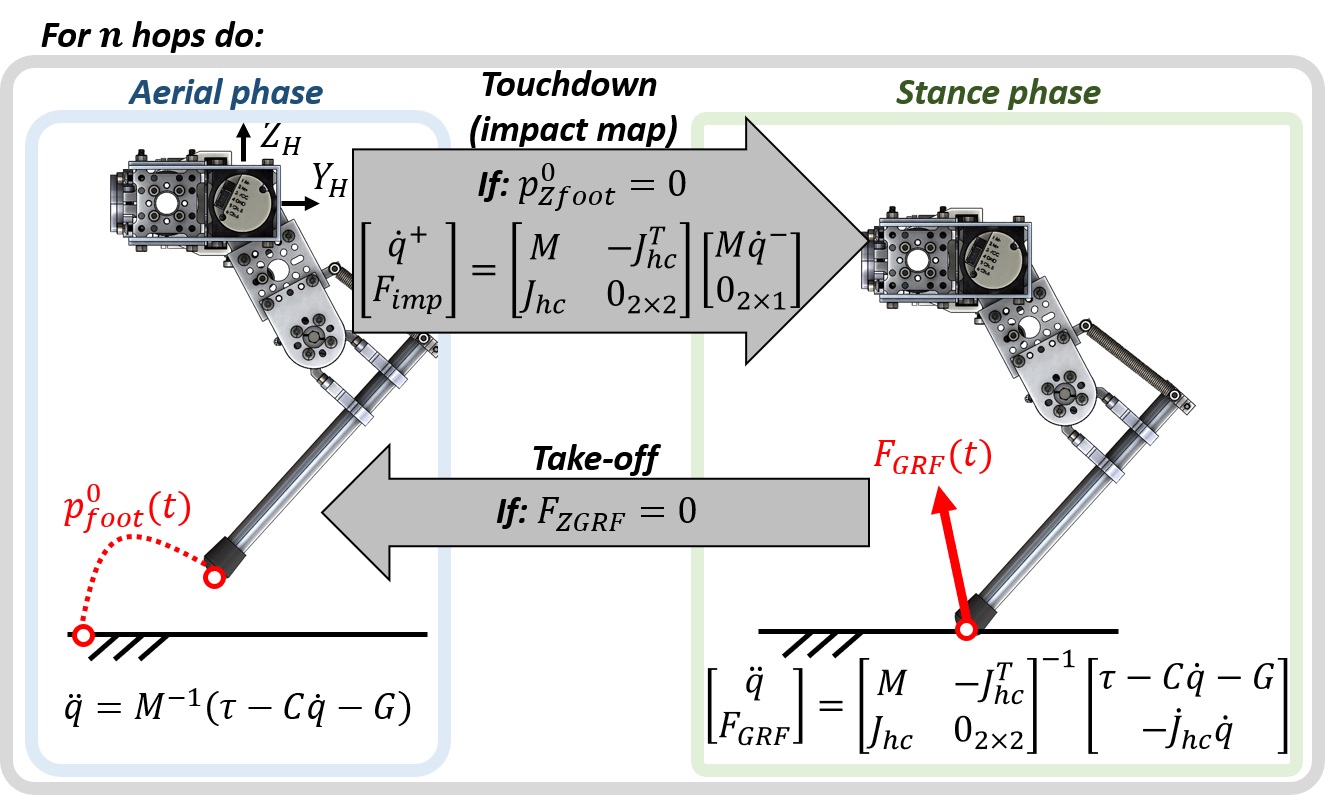
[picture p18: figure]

Fig. 3. Simulation loop of the hybrid dynamics of HOPPY for n hops. Continuous dynamics in flight (equation (3)) and stance (equation (14)) are interrupted by discrete events: touchdown and lift-off.

VII. HOPPING CONTROL FRAMEWORK
A challenging aspect of controlling hopping is that the foot experiences little resistance during aerial phase, but infinite resistance when touching the ground during stance phase. Hence, the controller must switch between different policies for the two scenarios. During aerial phase, the foot may follow a predefined trajectory to reach a desired stepping location at impact, as shown in fig. 3 left. However, during stance the foot pushes against the ground to apply a desired impulse to the CoM. Thus it is a common practice to perform position control of the leg during swing and force control of the ground contact force during stance. We employ a simple strategy in which, during flight, the leg holds a desired configuration and waits for touchdown, while, during stance, the foot applies a predefined force profile against the ground. An insightful and accessible discussion on hopping control is provided in [5], [7].
During flight phase, HOPPY simply holds a predefined leg configuration and waits for touchdown. To achieve this, we employ a simple task-space Proportional plus Derivative (PD) control using:

τaerial = J

T
c
Kp(p

H
ref − p

H
foot) − Kdp˙

H
foot
, (17)

where Jc(q) ∈ R

2×2
is the foot contact point Jacobian, which maps the joint velocities to the linear velocity of the foot in respect to the hip frame [ ˙y

H
foot z˙

H
foot]

T = Jc[

˙θH

˙θK]
T
In addition, Kp,d are diagonal and positive semi-definite proportional and derivative gain matrices, p

H
ref is the desired
position of the foot in respect to the hip at touchdown, and p

H
foot is its current value. The desired torques τaerial are mapped using the motor dynamics to the required input voltages uaerial:

uaerial =

"
Rw
kT NH

0
0

Rw
kT NK

τaerial + kv

"
NH

b˙θH

NK

b˙θK

. (18)

However, notice the positive feedback sign before kv and that b˙θH,K are the estimated joint velocities from an observer or

filtered derivative. Thus, overestimation of the speed constant kv or delay in the estimation of the joint velocities may cause

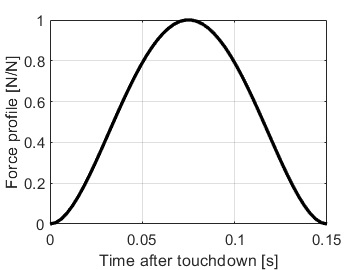
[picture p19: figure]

Fig. 4. Prescribed force profile for the horizontal (YH) and vertical (ZH) components of FGRF during a projected stance of 0.15s. The peak horizontal and vertical forces are modulated to control locomotion speed and hopping height, respectively.

oscillations or even instability. For the presented experiments we use a conservative approximation for the speed constant assuming kv ≈ 0.
During stance phase, the robot’s foot applies a predefined force profile against the ground, which results in an desired net impulse on the robot. The force profile can be generated using simple functions, such as polynomials, in order to be simple to compute online. Here we utilize Bezier polyno- ´ mials to create a force profile for a projected 0.15s stance duration as shown in fig. 4 [1]. The force peak is modulated to control jumping height and forward velocity. To apply the desired force against the ground, we map FdGRF to the desired joint torques using the contact Jacobian similarly to equation (17):

τstance = J

T
c FdGRF . | (19)

Equation (19) assumes that the motion of the lightweight leg does not significantly affect the body dynamics [7]. Otherwise, the control law would need to include the torque required to accelerate the leg mechanism using, for instance, Computed Torque Control [8]. Torque is mapped to input voltage using equation (18).
Finally, rapidly switching between the controllers for the stance and aerial phases can cause contact instability issues on the real robot. To smoothly transition between the two we command the input
u = αustance + (1 − α)uaerial, | (20)

in which α smoothly changes from 0 to 1 after touchdown within a predefined time, typically in the order of 10ms. This proposed control strategy is not affected by the leg singular configuration (straight knee) because it employs the transpose of the contact Jacobian, not its inverse. In addition, the simple strategy also does not require solving the robot inverse kinematics.

VIII. MECHATRONICS
The control of HOPPY involves fundamental concepts related to Mechatronics education. Including:
- Embedded systems: The robot controller runs in an onboard microcontroller (µC) which interfaces with the actuators, sensors, and the host computer.
- Discrete control: The µC performs computations and interfaces with peripherals at discrete time iterations.

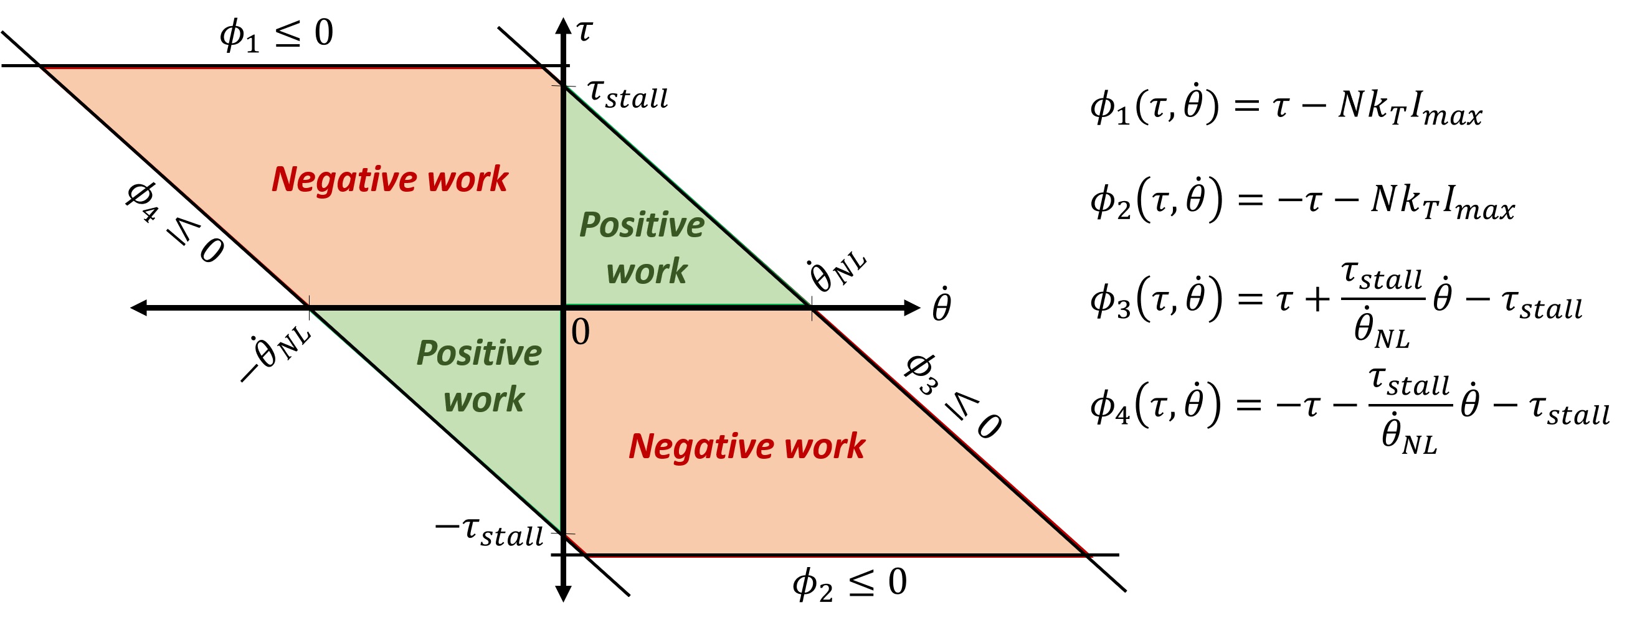
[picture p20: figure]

Fig. 5. Achievable torque (τ) and speed ( ˙θ) of the hip and knee joints. Functions φ1,2(τ, ˙θ) are defined by the gearbox ratio N, the torque constant kT , and the maximum current the driver can supply Imax. Functions φ3,4(τ, ˙θ) are defined by the voltage supplied Vmax, which limits the stall torque τstall =

| VmaxN Rw kT and no-load speed ˙θNL ≈ Vmax N kv
achievable by the joint. The operating region is larger for negative work (τ and ˙θ with opposite signals) due to the effect of the back-EMF.

And the deterministic execution of these events is fundamental for the implementation of discrete control policies. To effectively control dynamic motions, we target a control rate in the order of 1kHz (control loop of 1ms).
- Communication protocols: The µC regulates the motor voltage via Pulse Width Modulation (PWM), receives an analog signal which is proportional to the motor current, a binary signal for the foot contact switch sensor, and employs dedicated counters for the incremental encoders.
- Signal processing: The encoder has a coarse resolution of 28 counts per revolution (CPR) and the gearbox has noticeable backlash. To avoid noise amplification we estimate the motor velocity using a filtered derivative
θ˙(s)
θ(s) =

λs
λ+s

converted to discrete time with a period of T = 1ms, where s is the Laplace variable for frequency, and λ is a tunable constant (usually λ ≈ 10). Fast sampling rates are essential to avoid delayed velocity estimation. The analog signal from the motor current estimation is also noisy and requires filtering if used for controls.
- Input saturation: The achievable joint torques and speeds are limited by the available voltage supply (Vmax = 12V ) and the maximum current that the driver can provide (Imax = 30A) [6]. The operating region of the motors is depicted in fig. 5.

REFERENCES

[1] Y. Ding and H. Park. Design and experimental implementation of a quasi-direct-drive leg for optimized jumping. In 2017 IEEE/RSJ International Conference on Intelligent Robots and Systems (IROS), pages 300–305, Sep. 2017.
[2] Roy Featherstone. Rigid Body Dynamics Algorithms. Springer-Verlag, Berlin, Heidelberg, 2007.
[3] B. Katz, J. D. Carlo, and S. Kim. Mini cheetah: A platform for pushing the limits of dynamic quadruped control. In 2019 International Conference on Robotics and Automation (ICRA), 2019.
[4] G. Kenneally, A. De, and D. E. Koditschek. Design principles for a family of direct-drive legged robots. IEEE Robotics and Automation Letters, 1(2):900–907, July 2016.
[5] J. Koechling and H. Marc. How fast can a legged robot run? In Robots and Biological Systems: Towards a New Bionics? Springer Berlin Heidelberg, 1993.

[6] K. Lynch and F Park. Modern Robotics: Mechanics, Planning, and Control. Cambridge University Press, USA, 1st edition, 2017.
[7] M. H. Raibert. Legged Robots That Balance. Massachusetts Institute of Technology, USA, 1986.
[8] M. W. Spong. Robot Dynamics and Control. John Wiley and Sons, Inc., USA, 1st edition, 1989.
[9] R. Tedrake. Underactuated robotics: Algorithms for walking, running, swimming, flying, and manipulation (course notes for mit 6.832). downloaded on 09/09/2020 from http://underactuated.mit.edu/.
[10] E. Todorov. Convex and analytically-invertible dynamics with contacts and constraints: Theory and implementation in mujoco. In 2014 IEEE International Conference on Robotics and Automation (ICRA), pages 6054–6061, 2014.
[11] P. M. Wensing, A. Wang, S. Seok, D. Otten, J. Lang, and S. Kim. Proprioceptive actuator design in the mit cheetah: Impact mitigation and high-bandwidth physical interaction for dynamic legged robots. IEEE Transactions on Robotics, 33(3):509–522, June 2017.
[12] E. R. Westervelt, J. W. Grizzle, C. Chevallereau, J. H. Choi, and
B. Morris. Feedback control of dynamic bipedal robot locomotion. CRC press., 2007.

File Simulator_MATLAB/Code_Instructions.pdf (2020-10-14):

# Hopping Leg Simulator Instructions:

Yanran Ding and João Ramos

### 1. The Generation Function:

First you need to navigate to the folder “gen” and generate the kinematics and dynamic model by running the function “gen_dyn_boom_leg_v1.m”. It takes a while for the function to generate the files which will be located in the “gen” folder. In the following test, the “gen_dyn_boom_leg_v1.m” function will be referred to as the generation function. Further details are provided below:

The generation function uses the MALTAB symbolic Toolbox. The “define symbol” section defines the symbols that are used in the derivation. m_list_params is a list of all parameters. m_list_q and m_list_dq are the joint angle and joint velocities, respectively. m_list_dq is for the foot position at impact.

After the we calculate the Homogeneous Transformation Matrices (HTM), Jacobian matrices, Equation of Motion (EOM) matrices, etc., the write_fcn_m function writes a .m file that returns the instantaneous value of that matrix/vector. For instance, the function:

write_fcn_m('fcn_p_toe.m',{'q','p'},[m_list_q;m_list_params],{p_toe,'p_toe'});

writes a function fcn_p_toe.m that takes the joint angles q and the system parameters p to compute the x, y, and z spatial position of the foot. The files

write_fcn_m('fcn_De.m',{'q', 'p'},[m_list_q;m_list_params],{De,'De'});

write_fcn_m('fcn_Ce.m',{'q', 'dq', 'p'},[m_list_q; m_list_dq;m_list_params], {Ce,'Ce'});

are the function that return the inertia matrix De and Coriolis vector Ce of the manipulator with instantaneous configuration q and joint velocities dq. The actuation selection matrix Be maps the 2x1 control input vector you have access to (hip and knee torques) to the 4x1 input torque in the EOM. Remember that the first two joints are passive.

The generation function generates the .m files for all the required matrices that are going to be used for the computation of kinematics and dynamics of the manipulator in the main simulator.

### 2. The MAIN Simulation Function:

The main function for the simulation is named “MAIN.m” and is located at the root directory. There are several options that could be set in the MAIN function:

- p.Nstep: number of simulated hops
- p.isMotorDynamics: if the simulation includes the motor dynamics
- p.isControlSaturate: if torque saturation is considered

2.1. Parameters

The function “get_params.m” defines the parameters of the system, including:

- p.Tst: Nominal stance time for force parametrization during the stance phase
- p.Rboom: Boom radius
- p.g: gravity constant
- p. Fx_co_bz: Bezier polynomial coefficients for the ground reaction force (GRF)
- p.Kp & p.Kd: proportional & derivative gains for a PD controller
- p.Krh: constant for raibert hopper foot position heuristics
- p.N_animation: parameter for adjusting animation speeds
- p.M_r & p.B_EMF: motor dynamics
- p.uHip & p.uKnee: for control constraints
- Link lengths: HB,LB,DB,LH,LK,DK
- Link masses: M1,M2,M3,M4
- CoM position in link i frame: rxi, ryi, rzi
- Components of inertia tensor of link i: Jxxi, Jyyi, Jzzi, Jxyi, Jxzi, Jyzi
2.2. Dynamics and Transition Events

The hopping leg is a system with hybrid dynamics. This means that the dynamic are interrupted by discrete events (impacts with the grounds) that may cause discontinuous transition of the states (joint velocities). The system has different dynamic equations of motion during flight (foot not touching the ground) and during stance (foot in contact with the ground). The transitions between different dynamics are determined by the triggering of events, specifically, touch down (flight to stance) and lift off (stance to flight).

2.2.1.Flight Phase

The EoM for the flight phase is:

De

(q)q̈+ Ce

(q, q̇)q̇ + Ge

(q) = Beu

The actuation selection matrix Be is defined as

Be = [

0
0
1
0

0
0

0/1]

To make sure that joints 1 are 2 are passive (you can’t apply torque to them). A workspace PD controller is implemented to maintain the foot at a desired location.

Fsw = [

Kp1 | 0
0 | Kp2

] (pd − p) − [

Kd1 | 0
0 | Kd2

] ṗ

Then joint torque is calculated through the Jacobian mapping

u = J

T
(q) ⋅ Fsw

2.2.2.Stance Phase

The EoM for the stance phase is:

De

(q)q̈+ Ce

(q, q̇)q̇ + Ge

(q) = Jℎc

T FGRF + Beu

Jℎcq̈+ J̇
ℎcq̇ = 0

The second equation defines the holonomic constraint that the foot is in contact with the ground and cannot move (velocity of the foot is zero):

Jℎcq̇ = [

JYℎc
JZℎc

] q̇ = 0

The Jacobian Jℎc maps the joint velocities to the foot velocity in the directions YℎcZℎc
. This frame does not
necessarily coincide with the foot fixed frame. It changes at every stepping location. The direction Xℎc is
the radial direction between the foot and the boom base. Direction Zℎc
is vertical and always parallel with Z0. When the robot steps on the ground, the foot is not allowed to move vertically Zℎc or tangentially to the boom rotation Yℎc

. However, it can move radially towards the boom in the Xℎc direction. In readl life, the foot always slides a little bit in the Xℎc direction.

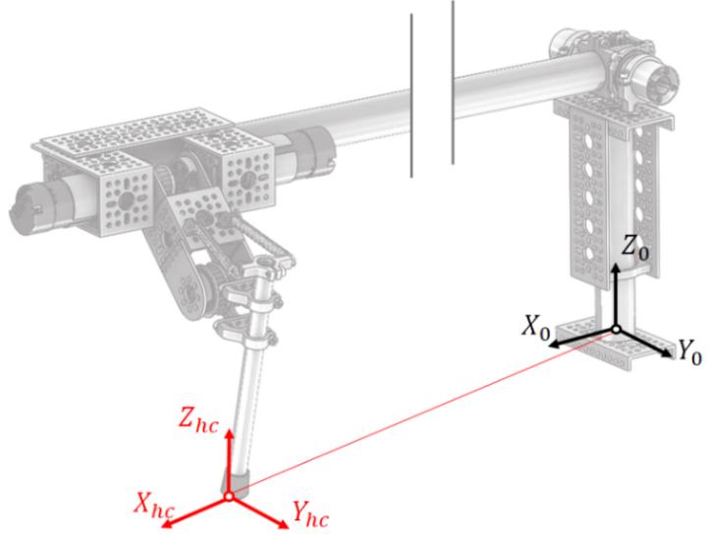
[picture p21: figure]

This means that the Jacobian Jℎc imposes a constraint to the foot motion. Taking the time derivative, we have:

Jℎcq̈+ J̇
ℎcq̇ = 0

Now we not only have to solve for the joint acceleration q̈at all the ode45 iterations, but we also need to compute the foot contact forces that make sure that the foot does not move. This model is called “Hard contact” model:
[
De | −Jℎc T
Jℎc | 02x2

][

q̈
FGRF

] = [

Beu − Ceq̇ − Ge
−J̇
ℎcq̇

]

[

q̈
FGRF

] = [

De | −Jℎc T
Jℎc | 02x2

]

−1
[

Beu − Ceq̇ − Ge
−J̇
ℎcq̇

]

The stance controller regulates the contact force between the foot and the ground. You can implement any force profile you want, but currently the for profile follows a Bezier polynomial parametrized in s ∈ [0,1] . The function polyval_bz(alpha, s) evaluates the force at instant s using Bezier coefficients alpha. Value of s is 0 at the beginning of stance and 1 at the end. For instance, for

s = 0:0.01:1;

plot(s,polyval_bz([0 0 60 0 0],s)

gives:

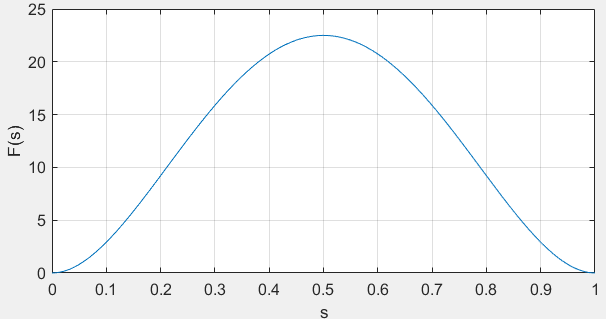
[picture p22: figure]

The stance controller now simply applies a force upwards to maintain hopping by using the foot Jacobian in respect to the hip JHIP. This Jacobian maps the relative velocity of the foot in respect to the hip. It’s the same Jacobian you developed for item 1.f) of milestone #1.

u = JHIP

T

[

FYd
FZd

] = JHIP
T

[

0
FBezier

]

You can change it to regulate hopping height, speed or the boom angle θ1. In addition, a soft joint PD controller is super-imposed to increase the robustness of the stance controller.

2.2.3.Transition Events

The touchdown event occurs when the foot height decreases to 0. This is defined in the function “event_touchDown(t,X,p)”. The current version of simulation only support flat ground. However, the users are encouraged to modify the touchdown event function to enable the hopping leg to traverse irregular terrains.

Because the foot impacts the ground and doesn’t bounce, we need to calculate what is the impact force applied to the robot that changes the velocity of the foot instantaneously. From, the joint velocities before

impact q̇

− we need to compute the joint velocities after impact q̇

+ and the impact Fimp. For that we us the function X_post = fcn_impactMap(X_prev,p) to solve the system:

M(q̇

+ − q̇

−) = Jℎc

T Fimp
Jℎcq̇

+ = 0

The liftoff event occurs when the ground reaction force in the vertical direction decreases to zero. For that we must monitor the z-component of FGRF obtained from solving the stance dynamics. In practice, a small threshold is used to declare liftoff event, which helps to increase the robustness of the simulation.

2.3. Animation

The animateRobot function takes int the logged data to produce an animation. If the bool value p.boolAnimate was set to 1, than a video file is going to be generated in the current directory, by the default name “video.mp4”. The following figure shows a snapshot of a hopping simulation.

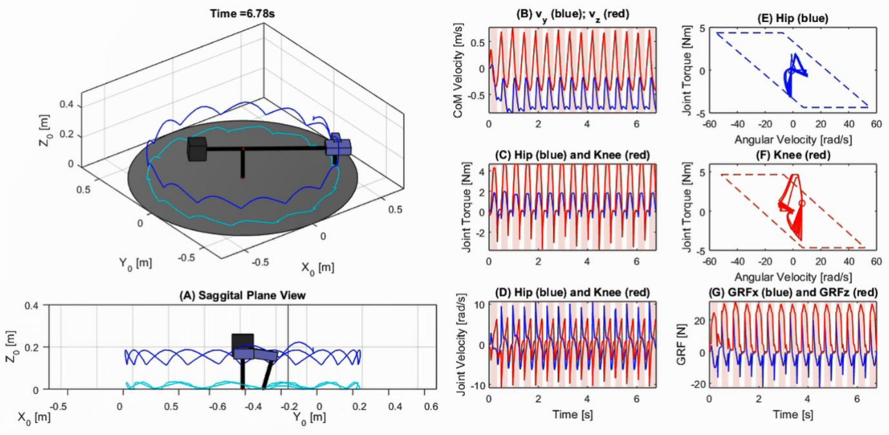
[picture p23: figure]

### 3. Summary

The simulation runs for a number of Nstep hops. It starts at flight (foot not touching the ground) and transitions to stance when touch down happens. The pseudocode of what happens is:

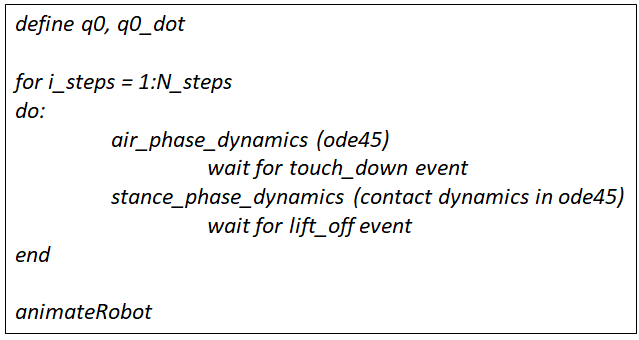
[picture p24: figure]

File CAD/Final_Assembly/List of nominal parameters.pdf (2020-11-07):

Nominal dimensions of HOPPY:

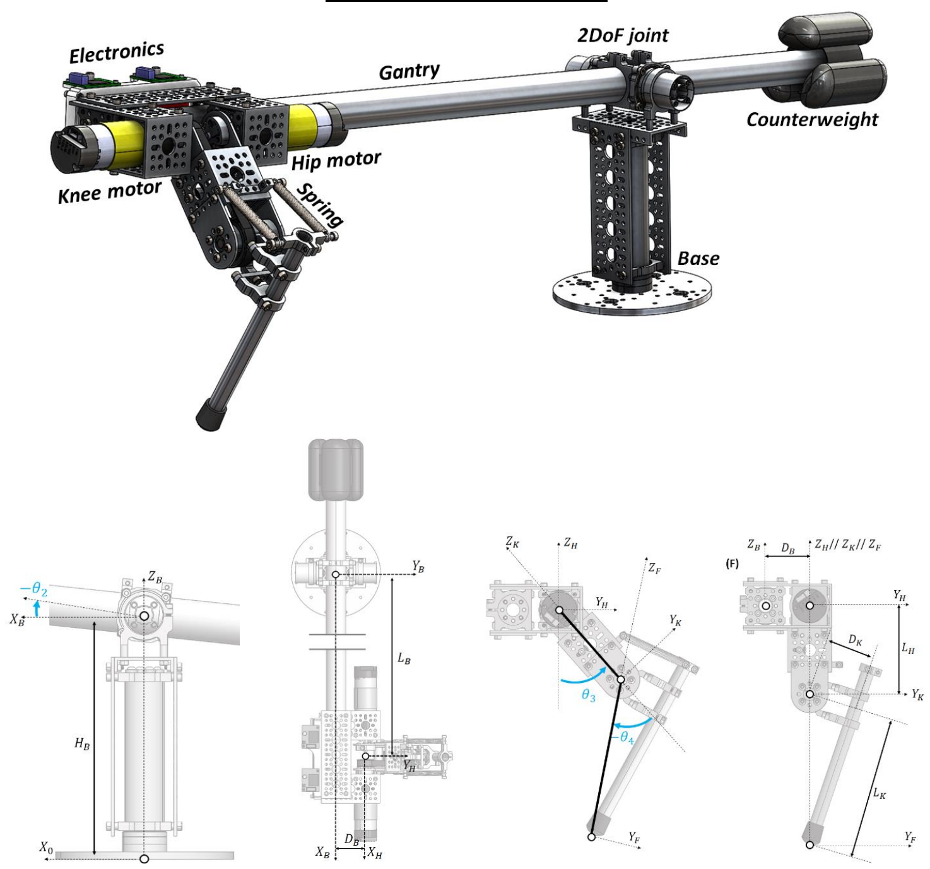
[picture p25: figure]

Parameter | Value [mm]
HB | 196.5
LB | 556
DB | 48
LH | 96
LK | 154.5
DK | 52

Rigid body parameters:

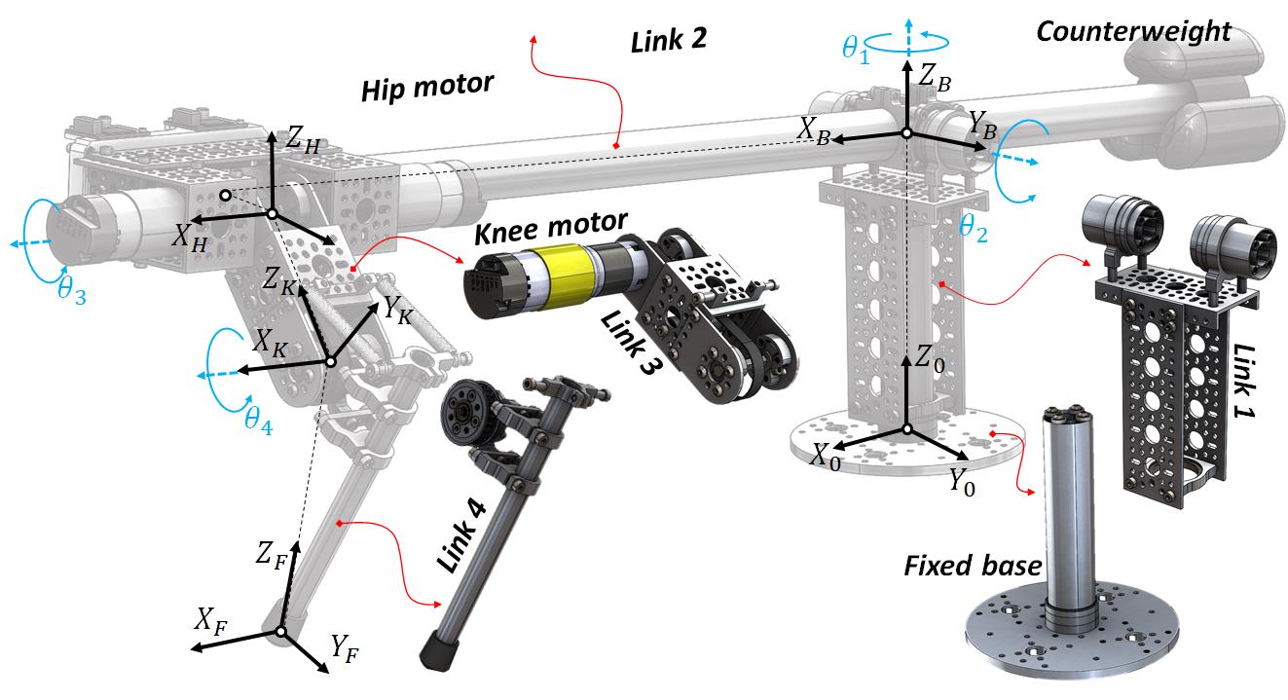
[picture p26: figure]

For each link i we list the total mass mi

in kg, the location of center of mass (CoM) in respect to the local frame in m, and the inertia tensor Ji taken at CoM and aligned with local coordinate frame in kg m²

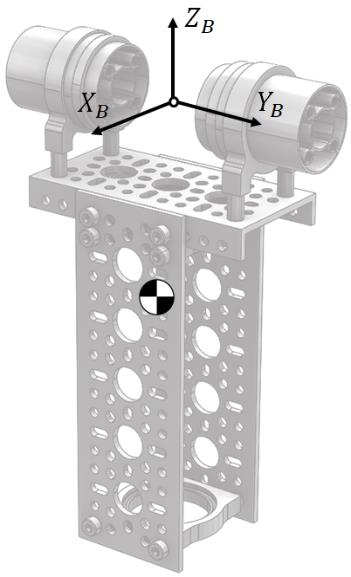
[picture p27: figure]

Link1:

m1 = 0.268
r1 = [

−0.00056660
0
−0.06176511

]

J1 = [

0.00115952 | 0 | −0.00000703
0 | 0.00104649 | 0
−0.00000703 | 0 | 0.00030518

]

Link 2:

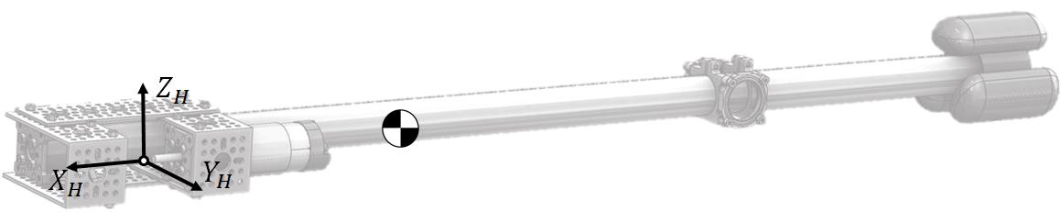
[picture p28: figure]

m2 = 2.365
r2 = [

−0.50195830
−0.03678363
0.00001342

]

J2 = [

0.00270252 | 0.01161483 | −0.00006434
0.01161483 | 0.30208952 | −0.00000838
−0.00006434 −0.00000838 | 0.30305924

]

Link 3:

m3 = 0.656
r3 = [

0.04825821
0.00027269
0.07708701

]

J3 = [

0.00082110 | −0.00002821 | 0.00058518
−0.00002821 | 0.00235762 | −0.00001795
0.00058518 | −0.00001795 | 0.00168340

]

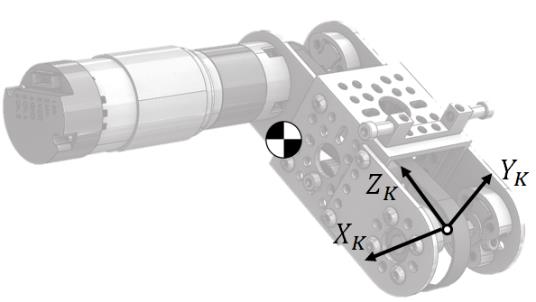
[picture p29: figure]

Link 4:

m4 = 0.149
r4 = [

0.00207136
0.02086667
0.14511501

]

J4 = [

0.00039424 | −0.00000379 −0.00000066
−0.00000379 | 0.00032191 | 0.00003269
−0.00000066 | 0.00003269 | 0.00010442

]

Actuator parameters:

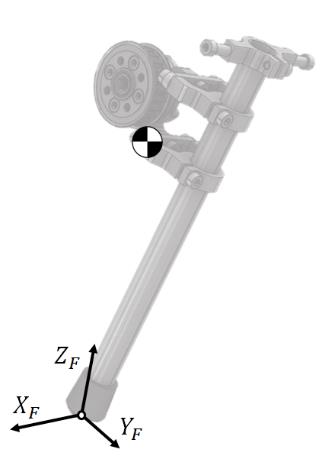
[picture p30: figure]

NH = 26.9 hip gearbox ratio
NK = 28.8 knee gearbox ratio
Ir = 7 × 10⁻⁶kg m² motor rotor inertia Rw = 1.3Ω motor winding resistance kT = 0.0135 Nm
A

brushed electric motor torque constant kv = 0.0186 V s
rad

brushed electric motor speed constant Vmax = 12V power supply voltage
Imax = 30A maximum (peak) current the motor driver can supply

Spring torque:

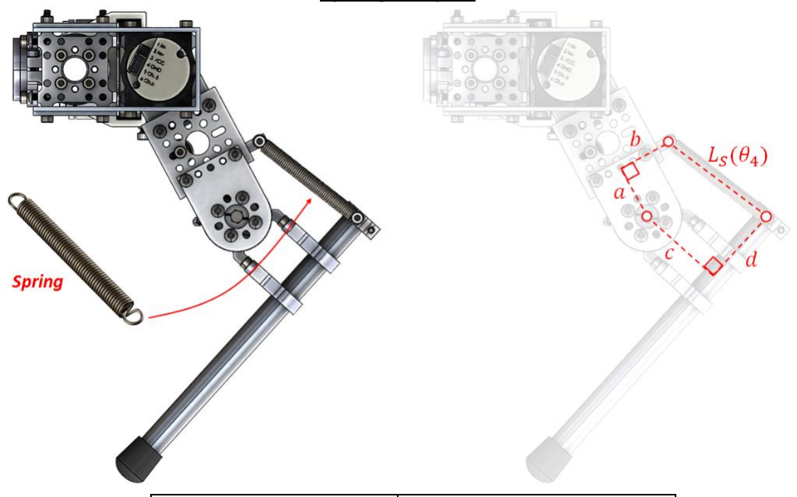
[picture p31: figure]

Length | Value [mm]
a | 32
b | 32
c | 52
d | 46 (nominal)
Approximate the spring length using a second order polynomial. The coefficients for Ls

(θ4

) will change
for different d values. For the nominal case:
Ls

(θ4

) ≈ a2θ4

2 + a1θ4 + a0
The torque per spring is given by: τs

(θ4

) =

∂Ls
∂θ4

Ks(L0 − Ls
(θ4

)) ≈ (2a2θ4 + a1
)Ks

(L0 − Ls

) for L0 ≤ Ls ≤ 120mm

Where:
a2 | −12.09
a1 | 10.75
a0 | 112.4
Spring constant Ks | 1.67kN/m
Resting spring length L0 | 80mm

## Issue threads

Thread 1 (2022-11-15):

Gantry Encoders

Remilarius, 2022-11-15:
Hi!

I'm a senior MechE working on my thesis and I decided to use HOPPY as a test platform.

All the parts on the BOM were bought and machined but as we were assembling it, we noticed that the CAD had two encoders that we didn't have on the BOM, one for the rotation position of the gantry/leg on the ground and one for rotation for the up/down of the leg. I was wondering if it was possible to get information on the parts in the encoder assemblies and if there was any information on the counterweight, as we didn't see any specifics.

YanranDing, 2022-11-24:
Hi,
If I remember correctly, for the gantry encoder you can use any incremental encoder. You can use pully for higher resolution.
There is no specifications on the counterweight. It could be gym weight or anything that is safe to be mounted to the end of the boom.

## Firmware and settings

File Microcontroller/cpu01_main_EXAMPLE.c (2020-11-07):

/*
This is the basic starter code for Hoppy's Leg

PLEASE NOTE! This is an example code that is NOT meant to run on the leg. It is meant to show the use of the program
While several functions and tools are included, many are not used in the simple example, but will probably be useful
when making the leg hop. This code should be used to test the motor functionality and as a starting place for writing
further code. The included run is a PD loop stepping the two   !!   DISCONNECTED   !!    motors back and forth.
Please clamp the motors down before testing the code! BE SAFE!

The code is broken into intuitive function blocks. The control loop runs at 1 kHz
Each function the user needs is listed below and well documented. All units should be NMS and rads
The starting point is the following function. This calls everything important.
If you are just gettings started,   !!!   START HERE   !!! and follow the code path down.

    DoEveryMilliSecond_CPU1                 - Line #368


At each time step the following functions are called:
    calculate_traj                          - Line # 208
    update_states                           - Line # 289    
    calculate_control();                    - Line # 322
    prevent_saturation();                   - Line # 342


Additional support functions include:
    get_avg_vel                             - Line # 241
    calculate_traj                          - Line # 208
    init_values                             - Line # 196
    get_phase                               - Line # 180    
    update_jacobian                         - Line # 272    
    pose_to_joint_space                     - Line # 281
    ADCD_ISR                                - Line # 620
    main                                    - Line # 410

OTHER
    - Update Encoder Positions. Search for this line. It will bring you to the point in the main function where
      the encoders are initilazized and offsets are set. This is important for zeroing the home position
                                            - Line # 507

    - Setup contact input. The code automatically reads the analog and the digital contact switch. 
      Further instructions are there. EDIT THIS FUNCTION BASED ON WHAT CONTACT METHOD YOU USE
                                            - Line # 180

    - General Declariation of Variables
                                            - Line # 107-175


If you have any questions, please contact Kevin Murphy or Joao Ramos

Enjoy Hoppy :)

@AUTHOR KEVIN MURPHY, Dan Block
kfmurph2@illinois.edu
*/

#include <math.h>

#include <xdc/std.h>
#include <xdc/runtime/Log.h>
#include <xdc/runtime/Error.h>
#include <xdc/runtime/System.h>

#include <ti/sysbios/BIOS.h>
#include <ti/sysbios/knl/Task.h>
#include <ti/sysbios/knl/Swi.h>
#include <ti/sysbios/knl/Clock.h>
#include <ti/sysbios/knl/Semaphore.h>
#include <ti/sysbios/family/c28/Hwi.h>

#include "F28x_Project.h"
#include "F2837xD_device.h"
#include "F2837xD_Ipc_drivers.h"

/***************************** Start Customized functions **************************/
#include "LCD.h"
#include "F28379D_Serial.h"
#include "F28379D_EPwm.h"     // for PWM signal
#include "F28379D_EQep.h"


//#include "driverlib.h"
//#include "device.h"
/*****************************  End Customized functions  **************************/

/*****************************    Start defined Values    **************************/
#define PI       3.1415926535897932384626433832795
#define TWOPI    6.2831853071795864769252867665590
#define HALFPI   1.570796326794897
/*****************************     End defined Values     **************************/

/*****************************  Start Simunlink plotting  **************************/
int adcb0result = 0; // 16-bit
int adcb1result = 0; // 16-bit
long read_1 = 0; // 32-bit
long read_2 = 0; // 32-bit
void simulink_serial_RXD(serial_t *s, char data);
#ifdef _FLASH
// These are defined by the linker (see device linker command file)
extern unsigned int RamfuncsLoadStart;
extern unsigned int RamfuncsLoadSize;
extern unsigned int RamfuncsRunStart;
#endif
extern eqep_t eqep1;
extern eqep_t eqep2;
/*****************************   End Simunlink plotting   **************************/

/****************************************************** OUR ADDITION START **********************************************************/
/******************************************************  User Definitions  **********************************************************/
// int16_t adcd0result = 0;
// int16_t adcd1result = 0;
int16_t analog_in[4] = {0,0,0,0};   // 16 bit analog between 0-3 V.
                                    // should have following index
                                    // [0] = touch sensor
                                    // [1] = optional th_1 encoder
                                    // [2] = optional th_1 encoder
                                    // [3] = open for user input

int16_t analog_limit = 2048;        // this is a tunable value that use used to measure analog linear contact
                                    // the value should be between 0-4096

//Physical dimensions
float LH = .0960;               // hip length
float DK = .0520;               // Knee offset
float LK = .1550;               // length of shank          !this values can be adjusted by the user!
float LKF;                      // shank effective length
float LHF;                      // Distance between hip and foot

//gains TODO TUNABLE VALUES
float Kp_a[2] = { 3000.,  3000.};   // Positional Gain for motor 1 and motor 2 in aerial phase
float Kd_a[2] = {  200.,   200.};   // Derivative Gain for motor 1 and motor 2 in aerial phase

float Kp_s = 60000.;                // Cartesian Positional Gain for motor 1 and motor 2 in stance phase
float Kd_s = 1000.;                 // Derivative Gain for motor 1 and motor 2 in stance phase

//control effort
float u[2]          = {0.0,  0.0};  // control effort for motor 1 and motor 2

//Joint States
float q_now [2]     = {0.0,  0.0};  // Position of the leg at Current time
float q_prev[2]     = {0.0,  0.0};  // Position of the leg at previous time step
float q_ref [2]     = {0.0,  0.0};  // Reference position for aerial
float err_q [2]     = {0.0,  0.0};  // Positional joint Error at current time step

float qdot_now [2]  = {0.0,  0.0};  // Current Joint Velocities
float qdot_prev[2]  = {0.0,  0.0};  // Previous Joint Velocities

//Cartesian States
float pos_des [2] = {0.0,   0.0};   // desired Cartesian position
float pos_now [2] = {0.0,   0.0};   // Current Cartesian position
float err_pos [2] = {0.0,   0.0};   // Positional Error at current time step
float vel_des [2] = {0.0,   0.0};   // desired Cartesian velocity
float vel_err [2] = {0.0,   0.0};   // Cartesian velocity error

// velocity filtering
int horizon = 3;
float vel_avgs[2][3];//YOU MUCH COPY THE HORIZON VALUE TO THE COL(2nd) ARRAY DIMENSION

//Switches
int phase = 1;  // Flag to tell which controller.
                //0 = aerial phase, 1 = stance phase

// Encoders
float enc_offset[2] = {0.0,0.0};    // offset for zeroing the encoders. Initialized in the original read,
                                    //so dont touch HERE. Check out  "Update Encoder Positions" in the Main function

//control Values
float T = 0.001;                    // sampling period in second. This should remain const
float J [2][2];                     //Jacobian

//Misc
long int cnt        = 0;            // time counter

// Temp trajectory vars. These are used in the given example trajectory. You can delete
int posref1dir = 0; // TODO comment out later - just used in initial demo
int posref2dir = 0; // TODO comment out later - just used in initial demo
/****************************************************** OUR ADDITION END **********************************************************/


/****************************************************** Start Supporting Functions **********************************************************/
void get_phase(void)
{
    /*This function reads the contact switch to determine phase.
     * if using additional encoders on th_1 and th_2, the user can
     * take the state readings and determine if the ground is being contacted here instead
     * */

    //USE THE FOLLOWING LINE IF YOU ARE USING A BINARY CONTACT SWITCH
    // phase =  GpioDataRegs.GPADAT.bit.GPIO9; // standing
    
    //Use the following line if you are using an analog linear potentiometer 
    phase = (analog_in[0] >= analog_limit);
    
    //If you are calculating contact based off of TH1 and TH2, do so here 
    // phase = f(th1, th2, th3, th4);
}
void init_values()
{
    /* This function defines any variable that has a function used in its declaration
     * There are some tunable values in here
     *
     * CCS compiler does not allow this to happen globally, so must be done in a function
     * which is big stoopid. But I digress
     * */

    //pos_des[0] = -0.07; // Reference position for aerial
    //pos_des[1] = -0.16; // Reference position for aerial
}
void calculate_traj(void)
{
    /*This function is used to determine the trajectory. This should be the first thing done in the timed loop
     * as it only depends on the discrete time. This function will eventually determine the phase (aerial or stance)
     * and choose the correct position required for that time in that phase*/

    //TODO replace with desired trajectory

    // motor1 control - step every 1/2 second
   if ((cnt%500) == 0 && posref1dir == 0)
   {
       q_ref[0] = PI;
       posref1dir = 1;
   }
   else if ((cnt%500) == 0 && posref1dir == 1)
   {
       q_ref[0] = 0;
       posref1dir = 0;
   }

   // motor2 control - step every second
   if ((cnt%1000) == 0 && posref2dir == 0)
   {
       q_ref[1] = PI;
       posref2dir = 1;
   }
   else if ((cnt%1000) == 0 && posref2dir == 1)
   {
       q_ref[1] = 0;
       posref2dir = 0;
   }
}

void get_avg_vel(float raw_vel_h, float raw_vel_k)
{
 /* This function puts the velocity measurements on the queue and finds the average over the past finite horizon.
  * This function should be passed the instantanious raw velocity and it automatically saves the average volocity
  * in the global variable. This is a simple example for data filtering
  */
    float sum_h = 0;
    float sum_k = 0;
    int i = 0;
    for (i = 0; i < horizon; i++)
    {// calculate average
        sum_h += vel_avgs[0][i];//hip
        sum_k += vel_avgs[1][i];//knee
    }
    sum_h += raw_vel_h;//hip
    sum_k += raw_vel_k;//knee

    i = 0;
    for (i = 0; i < horizon-1; i++)
    {   //pop and shift the queue
        vel_avgs[0][i] = vel_avgs[0][i+1];//knee
        vel_avgs[1][i] = vel_avgs[1][i+1];//hip
    }
    //add new value to end of the queue
    vel_avgs[0][horizon-1] = sum_h/(horizon+1);//knee
    vel_avgs[1][horizon-1] = sum_k/(horizon+1);//hip

    //save the joint velocities into global varibles
    qdot_now[0] = sum_h/(horizon+1);
    qdot_now[1] = sum_k/(horizon+1);
}
void update_jacobian(void)
{
    /*This function is given and will be useful when calculating anything in task space. This finds the jacobian*/
     // update jacobian
    J[0][0] = LH*cos(q_now[0]) + LKF*cos(q_now[0] + q_now[1]);
    J[0][1] = LKF*cos(q_now[0] + q_now[1]);
    J[1][0] = LH*sin(q_now[0]) + LKF*sin(q_now[0] + q_now[1]);
    J[1][1] = LKF*sin(q_now[0] + q_now[1]);
}
void pose_to_joint_space(void)
{
    //kinematics to get desired pose in joint space
    //calc after pos_des is found
    LHF = sqrt(pos_des[0]*pos_des[0] + pos_des[1]*pos_des[1]);      //length hip to foot
    q_ref[0] = (acos((LH*LH + LHF*LHF - LKF*LKF)/(2.*LH*LHF)) + atan2(pos_des[0],-pos_des[1]));
    q_ref[1] = -acos((LHF*LHF - LH*LH - LKF*LKF)/(2.*LH*LKF));
}
void update_states(void)
{
    /*This function updates the global state variables, such as position, velocity, and error for the robot
     * No arguments - all values are global. This function should be called after trajectory is determined
     * and before the control effort is calculated*/

    //states for motor 1
    q_prev[0] = q_now[0];                   // Shift time
    q_now[0] = read_Enc1() + enc_offset[0]; // Get actual position
    err_q[0] = q_ref[0] - q_now[0];         // Calculate positional error
    //float raw_vel_h = (q_now[0] - q_prev[0])/T; // Estimate Velocity
    qdot_now[0] = (q_now[0] - q_prev[0])/T;

    //states for motor 2
    q_prev[1] = q_now[1];                   // Shift time
    q_now[1] = read_Enc2() + enc_offset[1]; // Get actual position
    err_q[1] = q_ref[1] - q_now[1];         // Calculate positional error
    //float raw_vel_k = (q_now[1] - q_prev[1])/T; // Estimate Velocity
    qdot_now[1] = (q_now[1] - q_prev[1])/T;

    //OPTIONAL
    //update velocity in the finite horizon vel filter
    //get_avg_vel(raw_vel_h, raw_vel_k);

    // For stance controller
    update_jacobian();

    //get position in cartesian space
    pos_now[0] =  LH*sin(q_now[0]) + LKF*sin(q_now[0] + q_now[1]);//Cartesian position
    pos_now[1] = -LH*cos(q_now[0]) - LKF*cos(q_now[0] + q_now[1]);//from IK solve

}

void calculate_control(void)
{
    /*This function is our main control function. Whatever control algorithm we need should be done here.
     *This function should be called after trajectory/feed-forward is determined and states updated,
     *but before we check for saturation*/

    if (phase == 0) // Aerial Phase
    {   //Straigh PD control
        u[0] = Kp_a[0]*err_q[0] - Kd_a[0]*qdot_now[0];// desired zero velocity. still a normal PD contorller
        u[1] = Kp_a[1]*err_q[1] - Kd_a[1]*qdot_now[1];
    }
    else // Stance phase
    {
        //TODO WRITE YOUR STANCE CONTROLLER HERE :)
        // u[0] = 0;
        // u[1] = 0;
        u[0] = Kp_a[0]*err_q[0] - Kd_a[0]*qdot_now[0];// desired zero velocity. still a normal PD contorller
        u[1] = Kp_a[1]*err_q[1] - Kd_a[1]*qdot_now[1];
    }
}
void prevent_saturation(void)
{
    /*This function accesses global control effort variable and makes sure it isnt saturating the motors. No inputs or outputs required
     * This function should be called at the end of processing, directly before the commands are being sent to the motors*/
    // saturation protection

    //Torque_max_hip = 64.125 & Torque_max_knee = 69.7270
    //Torque mapping from 10 -> 69.7 and -10 -> -69.7

    u[0] = -(10/64.125) * u[0];//LERP torque commands from NM to [-10,10], 'pseudo pwm', which isbeing sent to the motor controllers
    u[1] =  (10/69.727) * u[1];//LERP torque commands from NM to [-10,10], 'pseudo pwm', which isbeing sent to the motor controllers

    //if outside of limits, set equal to closest limit
    if (u[0] >=  10) u[0] =  10;
    else if (u[0] <= -10) u[0] = -10;

    if (u[1] >=  10) u[1] =  10;
    else if (u[1] <= -10) u[1] = -10;
}

/******************************************************  End Supporting Functions  **********************************************************/


/******************************************************Start Every MS = Effective Main**********************************************************/
// For F28379D quadrature encoder counter
// control for speed control
void DoEveryMilliSecond_CPU1(void)
{
    //get Trajectory
    calculate_traj();
    //pose_to_joint_space();//THIS RUNS WHEN NOT USING JOINT SPACE CONTROL. UPDATE THIS IF YOU WANT TO USE IT

    //stance or aerial phase
    get_phase();

    //update states
    update_states();

    //Get the control effort
    calculate_control();

    //double check to make motors are not overcommanded
    prevent_saturation();

    //send commands to motors
    set_EPWM1A_VNH5019(u[0]);
    set_EPWM1B_VNH5019(u[1]);

    //increment time (ms)
    cnt++;

    // manually trigger the analog reading be calling the ADC ISR. You should not need to touch this
    AdcdRegs.ADCSOCPRICTL.bit.RRPOINTER = 0x10;
    AdcdRegs.ADCSOCFRC1.all |= 0x0F; //start conversion for 0,1,2,4
}
/******************************************************End Every MS = Effective Main**********************************************************/

// SYS/BIOS Clock function
void DoEverySecond_CPU1(void){
    GpioDataRegs.GPADAT.bit.GPIO31 ^= 1;

}


 
 
 

int main()
{
#ifdef _FLASH
    memcpy(&RamfuncsRunStart, &RamfuncsLoadStart, (size_t)&RamfuncsLoadSize);
#endif

    // Comment this when use CCS for debugging
    //#ifdef _FLASH
    //// Send boot command to allow the CPU2 application to begin execution
    //IPCBootCPU2(C1C2_BROM_BOOTMODE_BOOT_FROM_FLASH);
    //#else
    //// Send boot command to allow the CPU2 application to begin execution
    //IPCBootCPU2(C1C2_BROM_BOOTMODE_BOOT_FROM_RAM);
    //#endif

#ifdef _FLASH
    InitFlash();
#endif

    // Initialize System Control: PLL, WatchDog, enable Peripheral Clocks
    InitSysCtrl(); // F2837xD_SysCtrl.c

    // Initialize GPIO
    InitGpio(); // F2837xD_Gpio.c

    EALLOW;

    // For CPU1
    // Enable an GPIO OUTPUT on GPIO31, set it high
    GpioCtrlRegs.GPAPUD.bit.GPIO31  = 0;  // Enable pullup on GPIO31
    GpioDataRegs.GPASET.bit.GPIO31  = 1;  // Load output latch
    GpioCtrlRegs.GPAMUX2.bit.GPIO31 = 0;  // GPIO31 = GPIO31
    GpioCtrlRegs.GPADIR.bit.GPIO31  = 1;  // GPIO31 = output

/************************************************* SETTING UP CONTACT SWITCH **************************************************/
    // Enable an GPIO INPUT on GPIO9
    GpioCtrlRegs.GPAPUD.bit.GPIO9     = 0;    // enable pullup on GPIO9
    GpioCtrlRegs.GPAMUX1.bit.GPIO9    = 0;    // Set pin as standard GPIO as opposed to EPWM, etc
    GpioCtrlRegs.GPACTRL.bit.QUALPRD1 = 0x20; // Divide sampling frequency by 32. t_sample/32
    GpioCtrlRegs.GPADIR.bit.GPIO9     = 0;    // GPIO9 = input
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

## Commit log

2020-10-27 HOPPY - Bill of Materials
    This spreadsheet contains the list of components and quantities for the kit following the assembly instructions:
    https://youtu.be/CDxhdjob2C8
    [HOPPY_BoM.xlsx]
2020-11-07 add wiring diagram, c2000 processor, BOM
    [Kit BoM.xlsx]
2020-11-07 add CAD
    [1102-0005-0040.SLDPRT, 1102-0011-0088.SLDPRT, 1108-0001-0001.SLDPRT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]
2021-03-05 HOPPY technical manual
    This manual includes the kinematic and dynamics models used for HOPPY and a baseline hopping controller based on simple heuristics.
